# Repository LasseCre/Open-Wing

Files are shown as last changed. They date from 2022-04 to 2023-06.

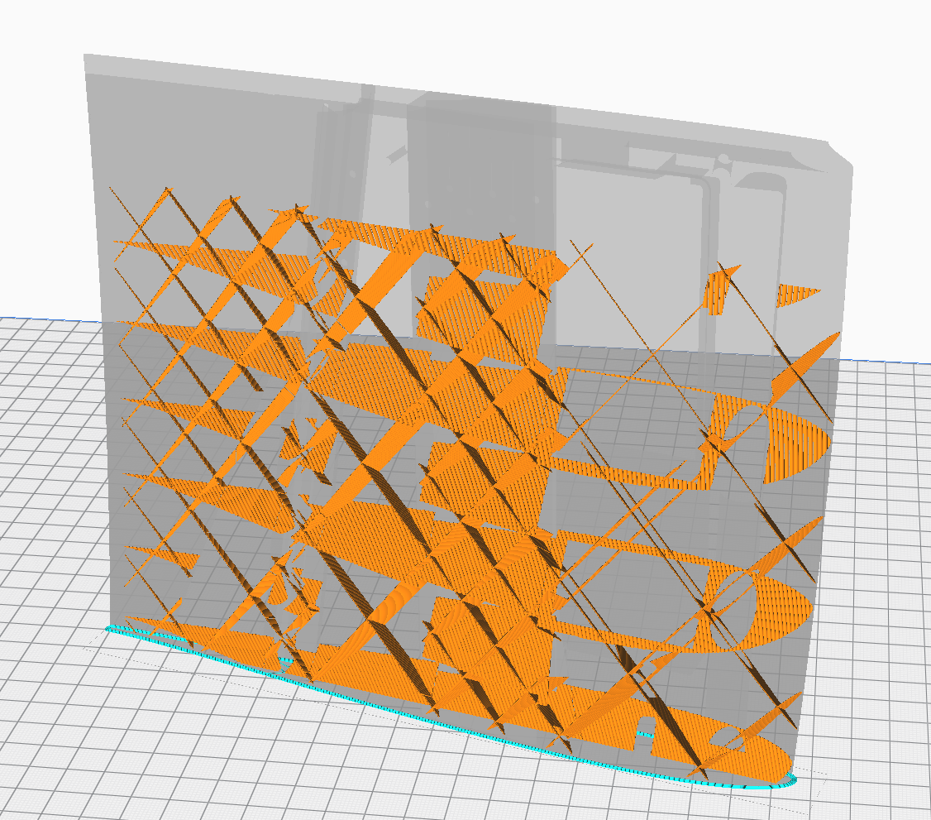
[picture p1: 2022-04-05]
General Data/Images/Cura Screenshot First Mesh Modifier_Infill only.png

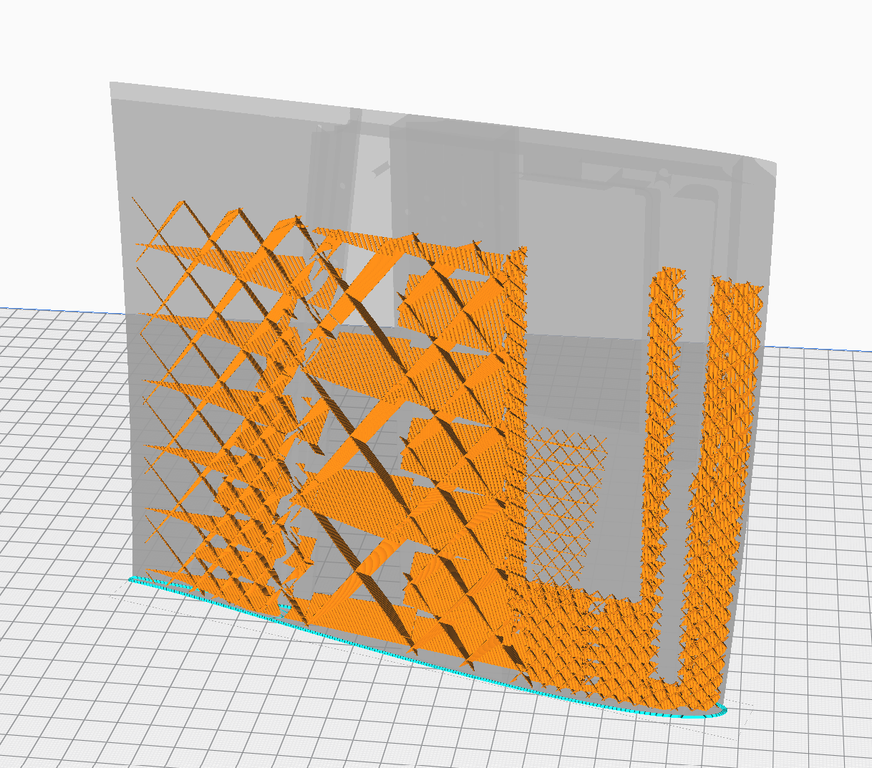
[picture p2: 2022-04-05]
General Data/Images/Cura Screenshot Third Mesh Modifier_Infill only.png

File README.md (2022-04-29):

# Open-Wing
## Documentation for a 3D printable open source rc glider
-----------------------------------------------------------------------------------------------------------
### Related Links:  
Thread in RCN: https://www.rc-network.de/threads/open-wing-ein-2m-allrounder-f%C3%BCr-jede-gelegenheit.11897828/  
Youtube Video: https://www.youtube.com/watch?v=wmPPW6raG3g&ab_channel=LasseC  
Contact me by opening an Issue here, or leave me a message at RC-Network or RC-Groups...  

### Overview
This is (becoming) the complete documentation for a 3d printable flying wing, including all the information that you need to print and build one yourself.
I recommend to read the general [Manual]('0_General%20Data/General%20Manual.md') before you start printing.

Style: Slightly swept plank  
Wingspan: 2000mm  
Weight: 1150 - 1600g (Depending on Configuration)  
Wingloading: 32g/dm^2 - 43g/dm^2  
Material: PLA
Print Time: Approx. 10 Days  
Small transport size (three part wing)  
Quadroflap  
Lots of carbon reinforcement  
Sailplane for now  
(Motor pod might be added later)  

### Structure
There are different versions available which differ in weigth and components, but they all share the same aerodynamic body.  
Therefore the data in the project is structured as follows:  

- **0_General Data** | *Everything that applies to all Versions*
- **V3_Slope** | *Sturdy and a little heavier, perfect for sloping and high speeds - Everything Ready!*
- **V4_Allround** | *The perfect wing to fly all the time, my personal favourite! - Available on demand*
- **V5_Convenience** | *Some measures taken, to make printing and assembly as easy as possible! - In Progress!*  
- **X_Deprecated** | *Old data that is kept only for nostalgic reasons*  

Please note that the Plane was previously called "Oso", which is still apparent in some of the file names  
This is a private project!

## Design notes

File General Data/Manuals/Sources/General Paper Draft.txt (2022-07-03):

OpenWing

Konstruktion und Bau von 3D-gedruckten Nurflügeln am Beispiel eines 2 Meter Seglers

3D-Druck stellt eine neue Fertigungsmethode dar, die in vielen Anwendungsbereichen neue Lösungen verspricht, so auch im Modellbau. Wie bei allen anderen Herstellungsmethoden gibt es jedoch verschiedene Vor- und Nachteile, die bei der Konstruktion möglichst gut ausgespielt, bzw. abgefangen werden sollten. In den letzten vier Jahren habe ich zahlreiche Nurflügelmodelle für die Herstellung mittels 3D-Druck konstruiert, gebaut und getestet, und möchte im folgenden meine Erfahrungen im Bezug auf dieses Herstellungsverfahren schildern. Der Fokus liegt hierbei eher darauf einen möglichen Weg zu zeigen, mit dem alltagstaugliche Modelle entstehen können, als darauf alle möglichen Konstruktionswege und 3D-Druckverfahren abzudecken.
Hierfür möchte ich am Beispiel des OpenWings, einem leicht gepfeiltem 2m Brett, den kompletten Ablauf von Konstruktion bis Erstflug einmal durchgehen. Die aerodynamische Auslegung von Nurflügeln wird nicht mit beschrieben, das vorliegen eines fertigen Entwurfs ist die Ausgangsvoraussetzung für den hier beschriebenen Ablauf.

Hier ein grober Überblick der verwendeten Parameter:
Nurflügelmodelle mit einer Spannweite von 900mm - 2000mm
Gewicht zwischen 250g - 2000g
Vorwiegend Segler (ohne Rumpf)

Fertig vorliegende aerodynamische Auslegung
Konstruktion mittels parametrischem CAD
Klassische Elektronik aus dem Modellbau
Herstellung mittels FDM Drucker
Materialmix aus PLA und CFK verstärkungen

Warum sollte man überhaupt ein Modell 3D-Drucken?
Das Bauen von Flugzeugen mittels 3D-Druck bietet einige Eigenschaften, die in ihrer Kombination interessante Vorteile gegenüber anderen Bauweisen bieten. So können mit 3D-Druck beispielsweise 3D-gekrümmte Oberflächen präziser als beim Positiv- oder Rippenbau hergestellt werden, ohne dabei den Kosten- und Arbeitsaufwand wie beim Bau aus Formen mit sich zu bringen. Außerdem lassen sich im 3D-Druck viele geometrische Features direkt im CAD umsetzen, so dass beim Aufbau wesentliche Arbeitsschritte, wie beispielsweise das Fräsen von Gestängedurchbrüchen, das Einkleben von Servorahmen, oder das Positionieren von Holmgurten, entfallen. Ein weiterer Aspekt ist, dass Dateien einfach ausgetauscht werden können, und somit die Zusammenarbeit and einem Projekt, oder auch das Nachbauen von Flugzeugen, global möglich wird. (Hierbei gibt es allerdings Einschränkungen durch die Verfügbarkeit von Anbauteilen, so sind zum Beispiel zöllische Schraueben oder CFK-Profile in Deutschland nur schwierig zu kriegen)
Andererseits gibt es jedoch auch einige wesentliche Nachteile, wie zum Beispiel die Einschränkungen, die durch die verfügbaren Materialien entstehen. Zumindest im FDM Druck lassen sich nur thermoplastische Kunststoffe (wenn auch teilweise mit kurzfaser Verstärkungen) drucken, bei denen das Verhältnis von Gewicht zu Festigkeit deutlich schlechter ist, als dies zum Beispiel bei CFK oder auch Fichtenholz oder Balsaholz, der Fall ist. Außerdem müssen alle wesentlichen geometrischen Oberflächen bereits im CAD mit konstruiert werden, da spontane Änderungen am fertigen Modell oft nur sehr schwer sauber umzusetzen sind.

Zusammengefasst nochmal die Vor- und Nachteile:
3D-gekrümmte Oberflächen können mit hoher Präzision hergestellt werden
Die Werkzeuge und das Verfahren sind sehr günstig
Es können sehr einfach Einzelstücke gebaut werden
3D-gedruckte Materialien haben ein schlechtes Gewichts / Festigkeitsverhältnis
3D-gedruckte Materialien sind sehr hitzeempfindlich

Um diese Frage zu beantworten, muss man sich die verschiedenen alternativen anschauen, von denen alle ihre Vor- und Nachteile haben, wobei natürlich auch persönliche Parameter, wie das Vorhandensein eines Druckers, oder eben einer Fräse, eine Rolle spielen. Wenn man bei der Arbeit eh eine 5-Achs Fräse stehen hat, die am Wochenende aus riesigen Alu-Reststücken perfekte Formen fräsen kann, und außerdem schon geübt im Umgang mit Faserverbundwerkstoffen ist, so ist 3D-Druck eher uninteressant. Wenn man jedoch eh einen 3D-Drucker hat und verschiedene Auslegungen vergleichend testen möchte, bevor man einen teuren Formensatz fräsen lässt, dann bietet sich 3D-Druck als günstige Testbauweise an. 

Um eine Einschätzung zu ermöglichen, habe ich verschiedene wesentliche Bauweisen in einer Tabelle zusammengefasst und nach mehreren Parametern bewertet. Hierbei wird sowohl die Konstruktion als auch der Bau betrachtet, notwendige Software wird als Werkzeug gewertet.

Parameter:
Einstiegshürden Material: Welche Werkzeuge / Anlagen sind notwendig?
Einstiegshürden Wissen: Wie schwierig ist der Bau, bzw. der Umgang mit den Werkzeugen?
Performance strukturell: Wie gut ist das Verhältnis von Gewicht zu Festigkeit?
Performance aerodynamisch: Mit welcher Genauigkeit lassen sich komplexe Oberflächen umsetzen?
Kosten + Kostenverlauf: Was kostet das erste Modell, was kosten nachfolgende Modelle?
Reproduzierbarkeit: Wie hoch ist der Aufwand für andere das Modell nachzubauen?
Beeinflussung der Umgebung: Braucht es eine Werkstatt, wird mit toxischen Substanzen gearbeitet?
Klassischer Einsatzbereich: Kurze Zusammenfassung des häufigsten Einsatzbereichs

Verfahren:					Rippe + Folie / Beplankung					EPP und co.					Positivbauweise Styro					Negativbauweise

Einstiegshürden Material: Unterschiedlich, Rippen können mit Freeware Tools gezeichnet und	Geringste Materialvoraussetzungen, fertig geschnittene	Hier ist der Aufwand für die Kerne ähnlich wie	Hohe Einstiegshürden, da allein das Material für				  von Hand geschliffen werden, dann sind jedoch nur einfache		Kerne können nach Maß online bestellt werden.		bei der Bauweise EPP und Co. Allerdings kommt	die Formen mehr kostet als so manches Modell.
			  Geometrieen mit beschränkter Genauigkeit möglich. Alternativ		Auch wenn man selber schneiden will, braucht man	dazu noch die Beschichtung mit einem 		Außerdem braucht man die Möglichkeit ein Urmodell
			  kann auch im CAD konstruiert und anschließend gelasert / gefräst	lediglich Schneidschablonen, einen Hiezdraht und	Faserverbundwerkstoff und / oder Holz, was	oder die Formen selber fräsen zu lassen, hinzu kommt
			  werden, dann braucht es mindestens eine Fräse / Laser, dafür		etwas Übung.						den Einsatz einer (einfachen) Presse oder eines	die manuelle Nachbearbeitung und das meistens eher
			  wird die Vervielfältigung einfacher. Außerdem benötigt man									Vakuumsystems voraussetzt.			teure Material für den Flieger selber.
			  neben "normalem" Werkzeug noch ein Folienbügeleisen.

Einstiegshürden Wissen:	  Gering, für einfache Geometrien ist kaum Vorwissen
			  erforderlich.

Performance strukturell:

Performance aerodynamisch:

Kosten + Kostenverlauf:

Reproduzierbarkeit:

Beeinflussung der Umgebung:

Klassischer Einsatzbereich:

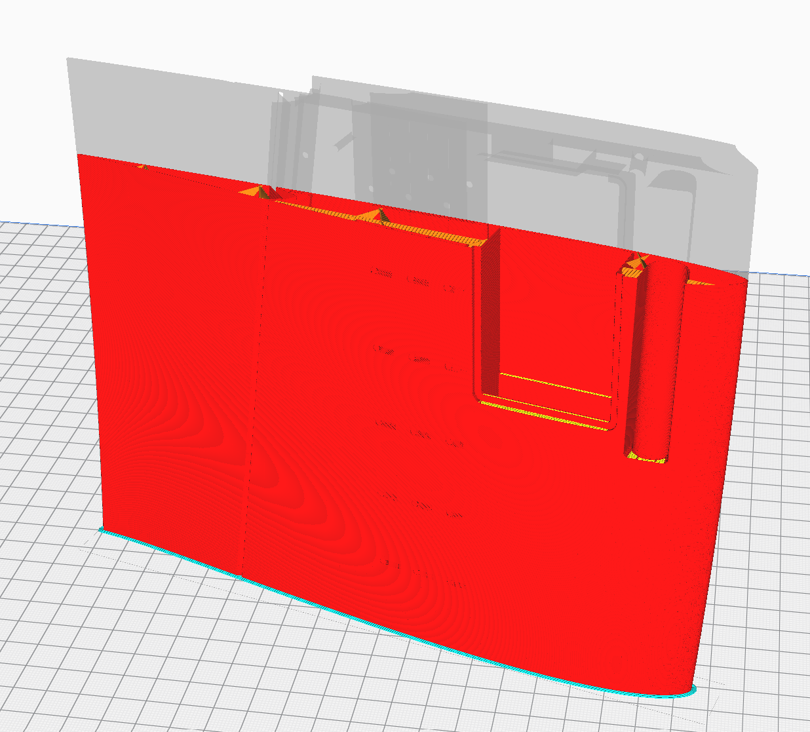
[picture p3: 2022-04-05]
General Data/Images/Cura Screenshot No Mesh Modifier.png

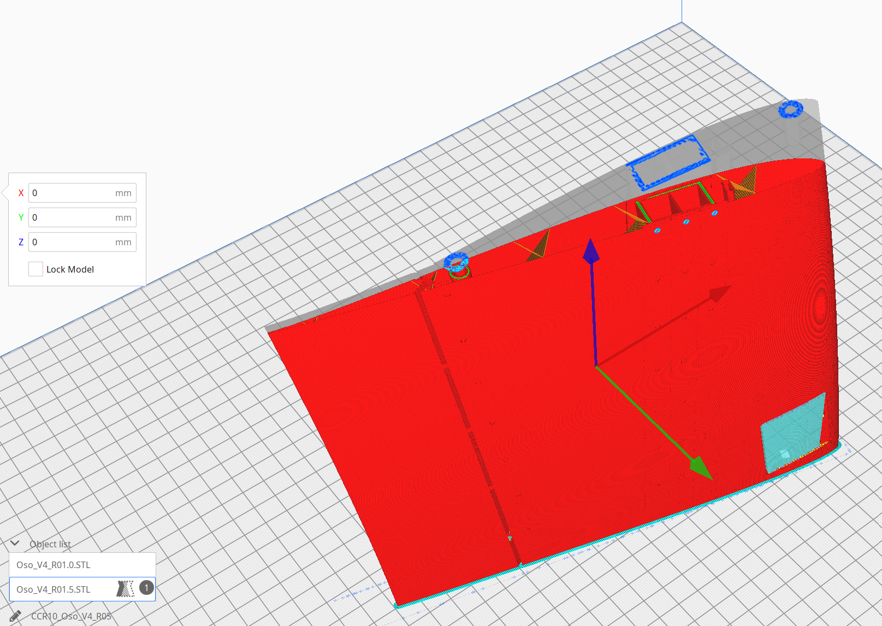
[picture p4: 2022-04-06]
General Data/Images/Two volumes Placement2.png

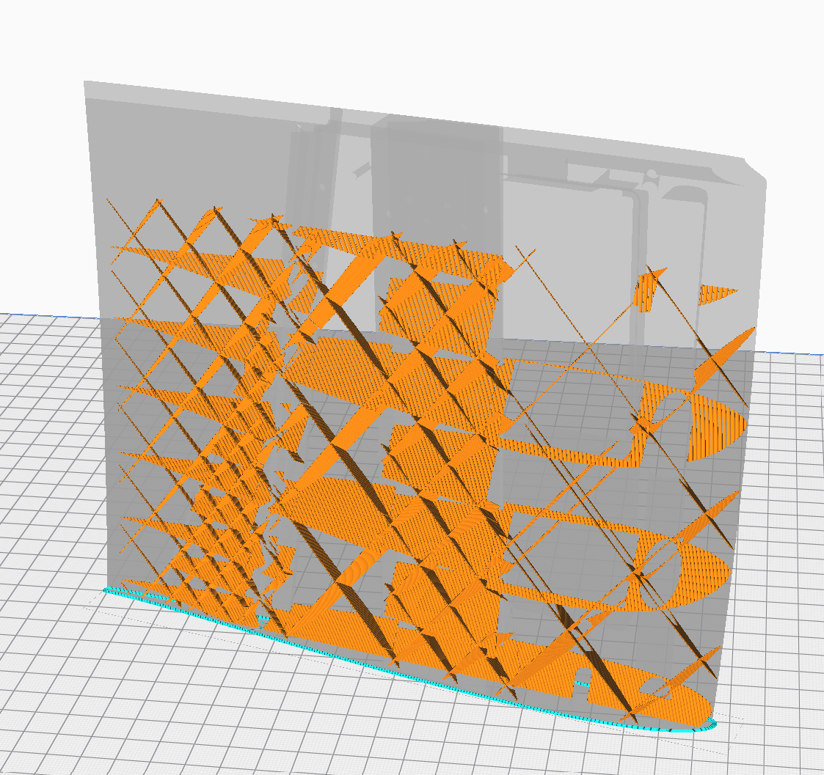
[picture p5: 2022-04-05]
General Data/Images/Cura Screenshot Second Mesh Modifier_Infill only.png

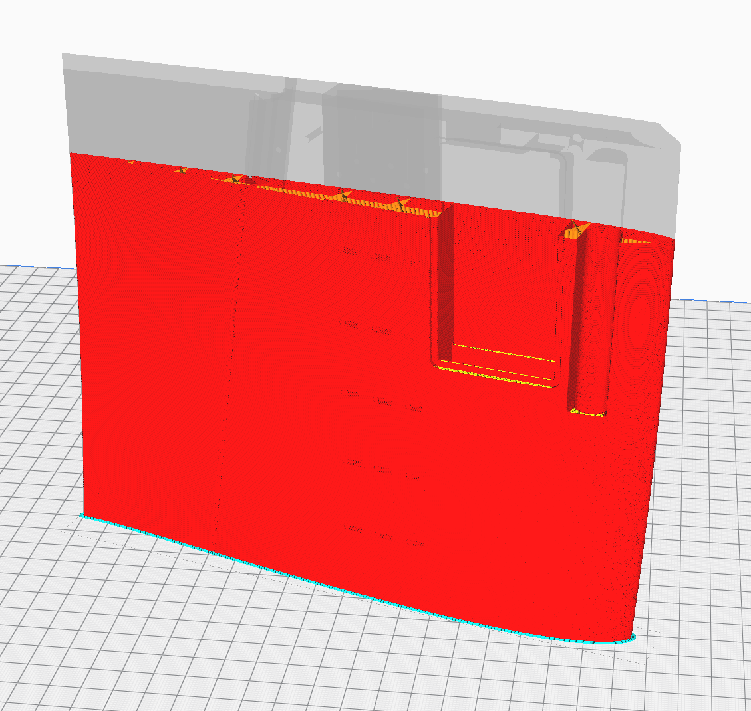
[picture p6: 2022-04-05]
General Data/Images/Cura Screenshot Second Mesh Modifier.png

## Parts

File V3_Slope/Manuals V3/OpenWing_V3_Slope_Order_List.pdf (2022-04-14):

# OpenWing_V3_Slope

### Oder List (EU)

Main spars

Wing joiners

Fuselage and stabilizer

Glue

For hinges

10 Pcs 0.5x10x1000mm rectangular carbon strip

2 Pcs 0.5x3x1000mm rectangular carbon strip

1 Pcs 0.6x5x1000mm rectangular carbon strip

10x10x1000mm rectangular carbon tube

4x100mm carbon tube

10/8x500mm pullwinded carbon tube

3x250mm carbon tube

20g thick CA glue | https://shop1.r-g.de/art/150120 Art.-Nr.: 1501202
2 Pcs 20g thin CA glue | https://shop1.r-g.de/art/150100 Art.-Nr.: 1501002

10 Pcs 1.2mm needles for application

1-3 Pcs syringe

Tape

Silikon (Bindulin Dichtfix) https://shop1.r-g.de/art/330155 Art.-Nr.: 3301552

https://shop1.r-g.de/art/330154
Art.-Nr.: 3301543

https://www.amazon.de/tesa-Malerband-einfache-Malerarbeiten-30mm/dp/B000VD8ZBW/ref=sr_1_5

https://www.amazon.de/Bindulin-Dichtfix-Fl%C3%BCssig-Gummi-Farbe-Com24/dp/B07DMQJTQP/ref=sr_1_16

8x250mm carbon tube

https://shop1.r-g.de/art/720003 Art.-Nr.: 7210005-100

https://shop1.r-g.de/art/720003 Art.-Nr.: 7203005-100

https://shop1.r-g.de/art/720003 Art.-Nr.: 7205006-100

https://shop1.r-g.de/art/750302 Art.-Nr.: 7510091

https://shop1.r-g.de/art/604070
Art.-Nr.: 64040030-100

https://www.carbonscout-shop.de/CFK-Carbon-Rohr-10x8x1000mm-Pullwinding.html

https://shop1.r-g.de/art/604070 Art.-Nr.: 64030020-100

https://shop1.r-g.de/art/604070 Art.-Nr.: 64080060-050

1/2

# OpenWing_V3_Slope

### Oder List (EU)

2/2

Electronics

Servo connections

Ballast Material

Option:
4 Pcs KST X10-mini

Option:
4 Pcs Kingmax 0612W 10mm HV-Servo

Option:
4 X-612 Servo

Y cable for batteries

2 Pcs battery for 2S2P

4 Pcs Cables for Servos

4 Pushrod M2

4 Pcs „Alu Gabelkopf M2“

2-3 Pcs 10x100mm K10 tungsten steel https://www.f3x.de/kst-x10-mini-v8-10mm-digitaleshv-servo-bis-75-ncm

https://www.mg-modellbau.de/Servos/Kingmax/Servo-Kingmax-10mm-HV-Servo-54-85kgcm-50-84V-Digital-Uni-Stecker.html
https://www.f3x.de/x-612-10mm-hv-servo-bis-85-ncm-coreless-digital

https://www.conrad.de/de/p/modelcraft-parallel-kabel-1x-bec-buchse-2x-bec-stecker-10-00-cm-0-25-mm-208423.html

https://www.conrad.de/de/p/reely-modellbau-akkupack-lipo-7-4-v-600-mah-zellen-zahl-2-15-c-softcasebec-buchse-1614803.html

https://www.amazon.de/YIXISI-Verl%C3%A4ngerungskabel-Stecker-Fernbedienung-Flugzeug/dp/B08JVBYS8L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

https://www.f3x.de/alu-gabelkopf-23mm-gewindem2

https://www.ebay.de/itm/402851236392https://www.f3x.de/stahl-schubstange-1,7-mm-x-200-mm-mit-teilgewinde-m2

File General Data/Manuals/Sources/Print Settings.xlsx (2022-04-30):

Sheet: Printsettings_General
Layer Height | 0.16
Line Width | 0.38
Wall line count | 1
Top Layers | 2
Bottom Layers | 2
Outer before inner walls | X
Compensate wall overlaps | X
Compensate inner wall overlaps | X
Compensate outer wall overlaps | X
Fill gaps between walls | Nowhere
Infill before walls | OFF!
Infill overlap percentage | -35%
Z-Hop when retracted | X
Z-Hop height | 0.4
Support | X
Build plate adhesion | Brim
Brim line count | 4

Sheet: Printsettings_V3_Slope
Part | Main | Modifier | Width | Wall count | Infill | Top | Bottom | Weight (L+R)
R05.0 | X |  | 0.38mm | 1 | 3.50% | 2 | 2 | 37g
R05.1 |  | X |  |  | 7%
R05.2 |  | X |  | 1 | 14%
R04.0 | X |  | 0.38mm | 1 | 3.50% | 2 | 2 | 80g
R04.1 |  | X |  |  | 7%
R04.2 |  | X |  |  | 14%
R04.3 |  | X |  | 1 | 14%
R03.0 | X |  | 0.38mm | 1 | 3.50% | 2 | 2 | 141g
R03.1 |  | X |  |  | 7%
R03.2 |  | X |  |  | 14%
R03.3 |  | X |  | 1 | 14%
R03.4 |  | X |  | 2 | 28% | 2 | 2
R03.Block |  | Support Blocker
R02.0 | X |  | 0.38mm | 1 | 3.50% |  |  | 170g
R02.1 |  | X |  |  | 7% | 1
R02.2 |  | X |  |  | 14%
R02.3 |  | X |  | 2 | 14% | 2
R02.4 |  | X |  | 100
R01.0 | X |  | 0.38mm | 1 | 3.50% |  |  | 207g
R01.1 |  | X |  |  | 7% | 1
R01.2 |  | X |  |  | 14%
R01.3 |  | X |  | 3 | 28% | 5 | 5
R01.4 |  | X |  | 100
R01.Block |  | Support Blocker
R00.0 | X |  | 0.38mm | 1 | 3.50% |  |  | 245g
R00.1 |  | X |  |  | 7% | 1
R00.2 |  | X |  |  | 14%
R00.3 |  | X |  | 3 | 28% | 5 | 5
R00.4 |  | X |  | 100
SLW00.0 | X |  | 0.38mm | 1 | 3%
SLW00.1 |  | X |  |  | 6%
SLW01.0 | X |  | 0.38mm | 1 | 3%
SLW01.1 |  | X |  |  | 6%
Covers | X |  | 0.4mm | 1 | 10% | 4 | 2
Servo Horns | X |  | 0.4mm | 50
Helling | X |  | 0.4mm | 2 | 10% | 4 | 4

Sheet: Printsettings_V5_Community
Part | Main | Modifier | Width | Wall count | Infill | Top | Bottom | Weight (L+R)
R05.0 | X |  | 0.38mm | 1 | 3.00% | 2 | 2 | 34g
R05.1 |  | X |  |  | 6%
R05.2 |  | X |  |  | 12%
R04.0 | X |  | 0.38mm | 1 | 3.00% | 2 | 2 | 75g
R04.1 |  | X |  |  | 6%
R04.2 |  | X |  |  | 12%
R04.3 |  | X |  |  | 12%
R03.0 | X |  | 0.38mm | 1 | 3.00% | 2 | 2 | 139g
R03.1 |  | X |  |  | 6%
R03.2 |  | X |  |  | 12%
R03.3 |  | X |  | 2 | 24% | 2 | 2
R03.Block |  | Support Blocker
R02.0 | X |  | 0.38mm | 1 | 3.00% |  |  | 164g
R02.1 |  | X |  |  | 6% | 1
R02.2 |  | X |  |  | 12%
R02.3 |  | X |  | 2 | 12% | 2 | 2
R02.4 |  | X |  | 3 | 36% | 2 | 2
R01.0 | X |  | 0.38mm | 1 | 3.00% |  |  | 191g
R01.1 |  | X |  |  | 6% | 1
R01.2 |  | X |  |  | 12%
R01.3 |  | X |  | 2 | 24% | 2 | 2
R01.4 |  | X |  | 3 | 36% | 2 | 2
R01.Block |  | Support Blocker
R00.0 | X |  | 0.38mm | 1 | 3.00% |  |  | 203g
R00.1 |  | X |  |  | 6% | 1
R00.2 |  | X |  |  | 12%
R00.3 |  | X |  | 2 | 24% | 2 | 2
R00.4 |  | X |  | 100
SLW00.0 | X |  | 0.35mm | 1 | 3% |  |  | Complete 24g
SLW00.1 |  | X |  |  | 6%
SLW01.0 | X |  | 0.35mm | 1 | 3%
SLW01.1 |  | X |  |  | 6%
Covers | X |  | 0.38mm | 1 | 20% | 2 | 2 | 20g
Servo Horns | X |  | 0.38mm | 50
Helling | X |  | 0.4mm | 2 | 10% | 4 | 4

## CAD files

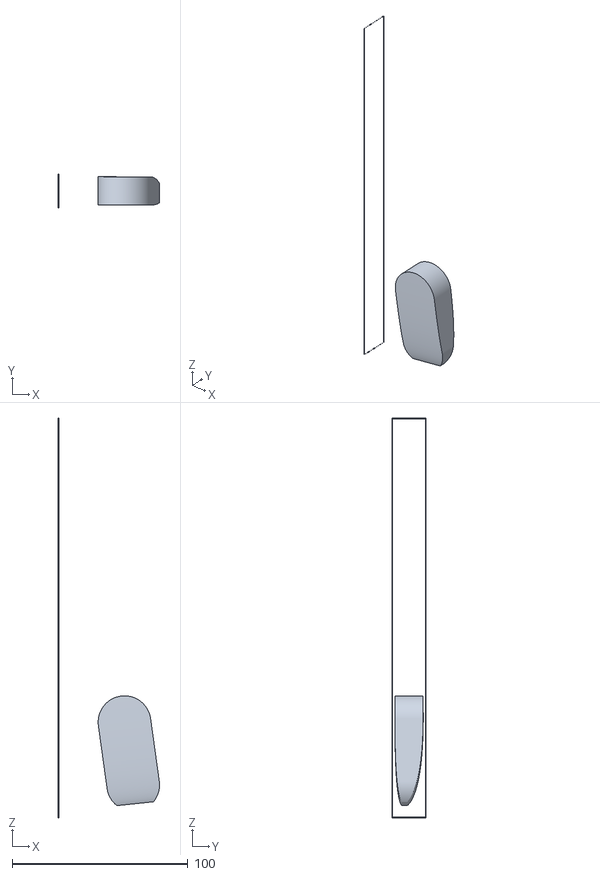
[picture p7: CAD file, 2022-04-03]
CAD/Export/V1/Oso_R01/Oso_R01.6.STL
57.5 x 19.0 x 227.0

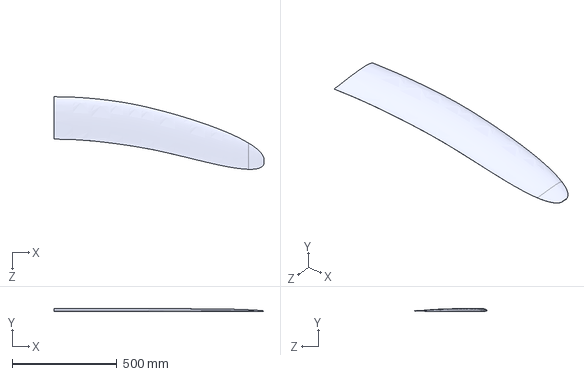
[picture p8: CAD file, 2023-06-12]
General Data/3D/OpenWing_Clean Volume.STEP
1000.0 x 16.4 x 346.0 mm

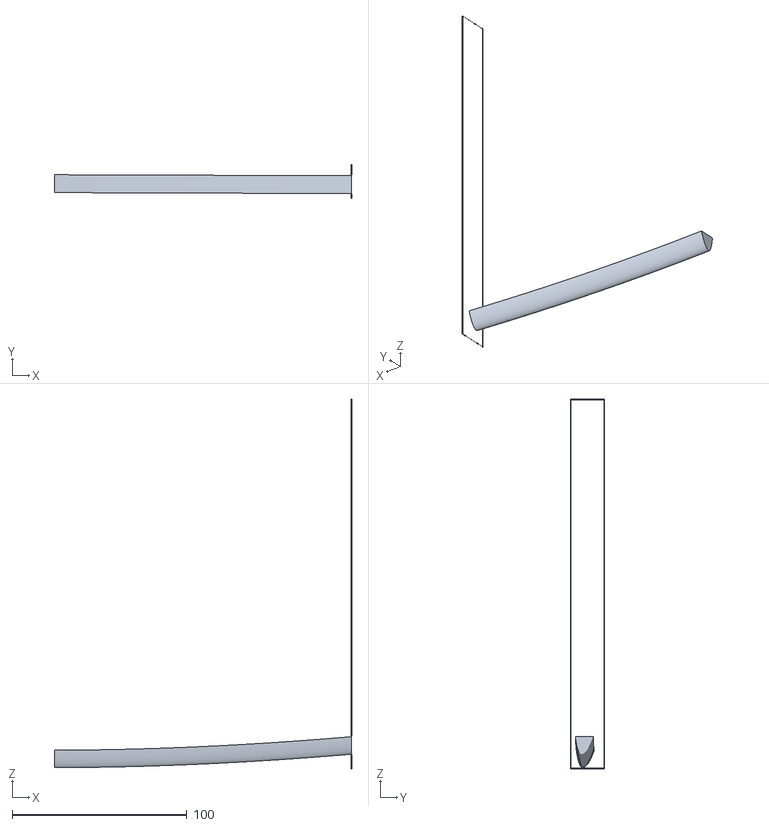
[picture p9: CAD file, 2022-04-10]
V3_Slope/3D/STL/OpenWing_V3_Slope_R00/OpenWing_V3_Slope_R00.4.STL
170.0 x 19.0 x 211.0

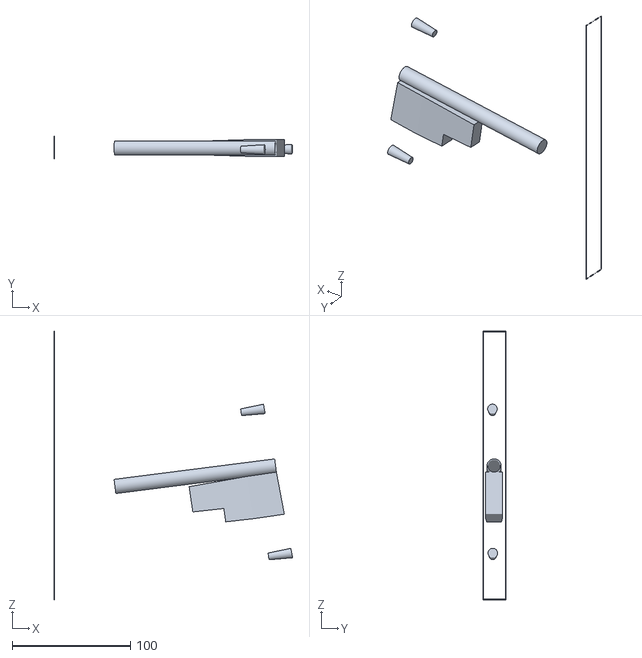
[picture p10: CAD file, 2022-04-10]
V3_Slope/3D/STL/OpenWing_V3_Slope_R01/OpenWing_V3_Slope_R01.4.STL
201.9 x 19.0 x 227.0

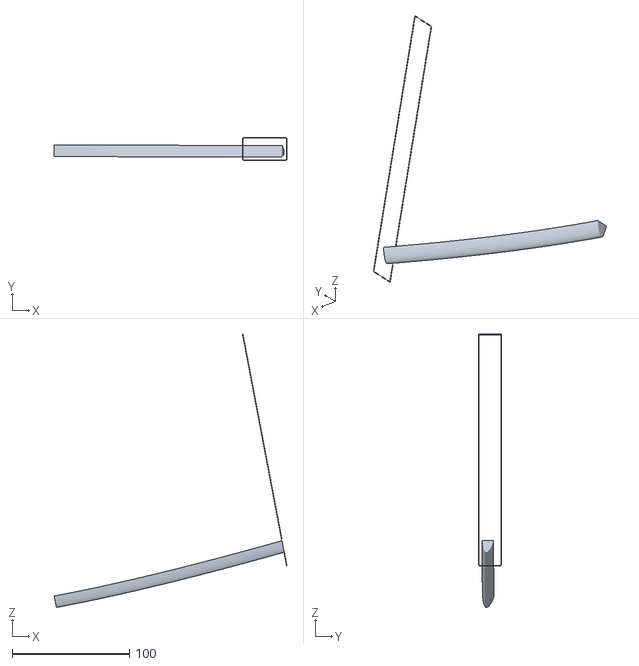
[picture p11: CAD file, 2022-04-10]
V3_Slope/3D/STL/OpenWing_V3_Slope_R02/OpenWing_V3_Slope_R02.3.STL
198.7 x 19.0 x 233.1

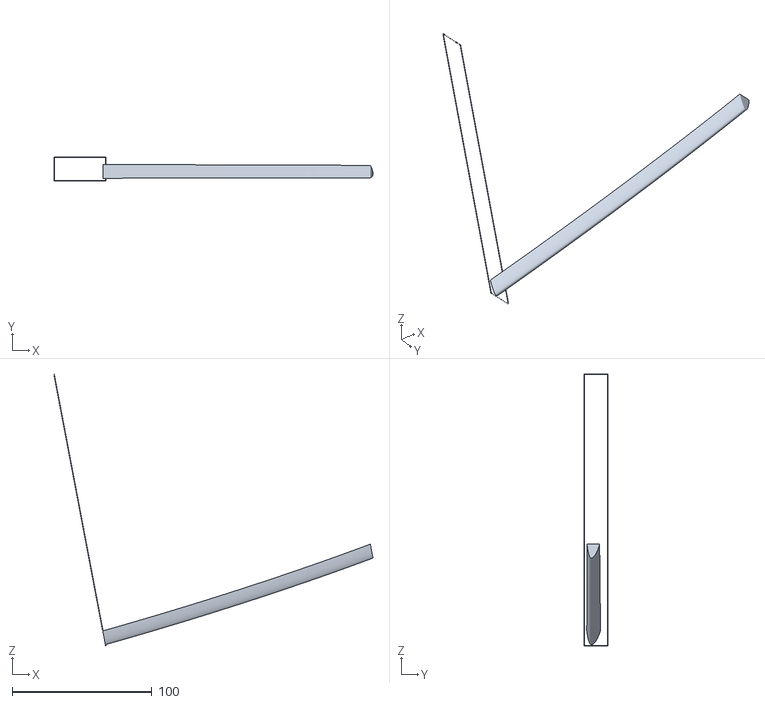
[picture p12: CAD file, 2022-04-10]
V3_Slope/3D/STL/OpenWing_V3_Slope_R03/OpenWing_V3_Slope_R03.3.STL
228.6 x 17.0 x 194.6

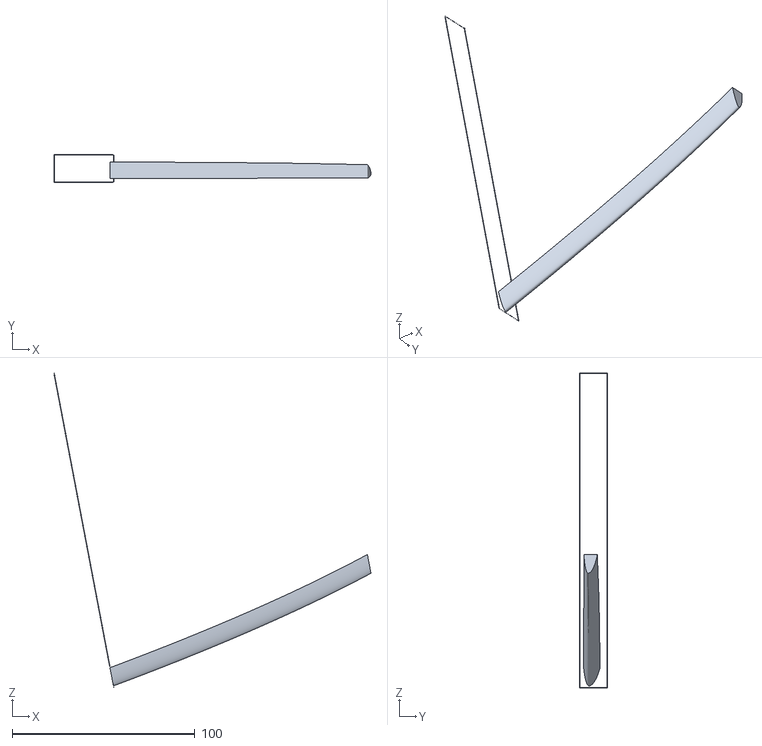
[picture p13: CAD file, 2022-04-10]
V3_Slope/3D/STL/OpenWing_V3_Slope_R04/OpenWing_V3_Slope_R04.3.STL
173.5 x 15.0 x 172.0

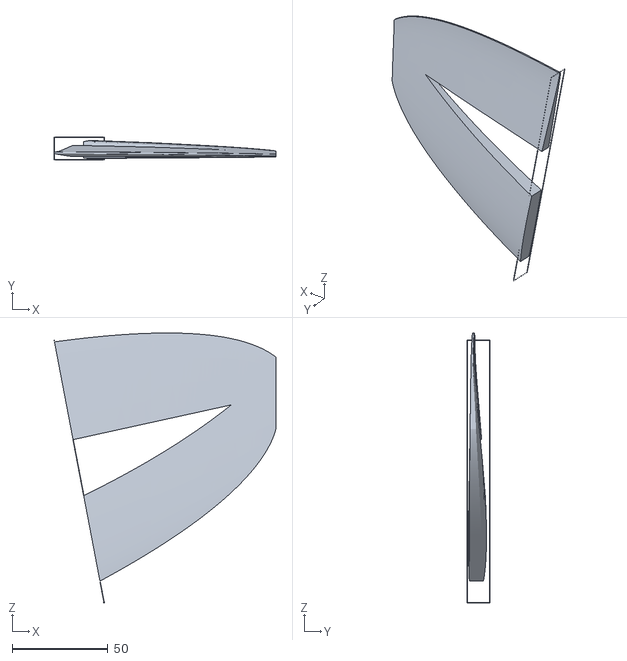
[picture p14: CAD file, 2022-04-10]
V3_Slope/3D/STL/OpenWing_V3_Slope_R05/OpenWing_V3_Slope_R05.1.STL
116.0 x 12.0 x 141.2

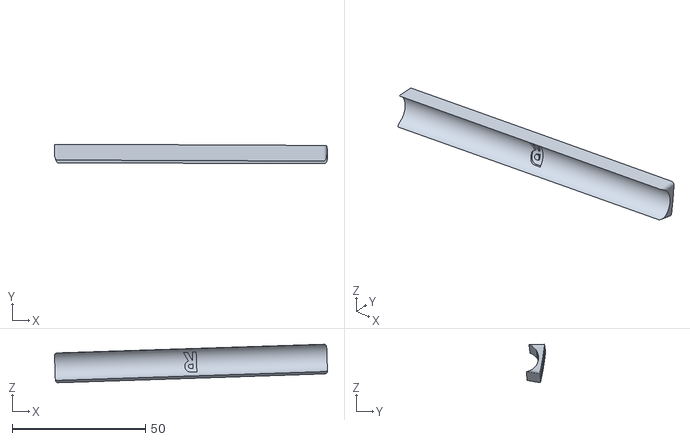
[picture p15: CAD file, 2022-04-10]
V3_Slope/3D/STL/OpenWIng_V3_SLope_SmallParts/OpenWing_V3_Slope_BallastCover.STL
102.4 x 7.13 x 14.5

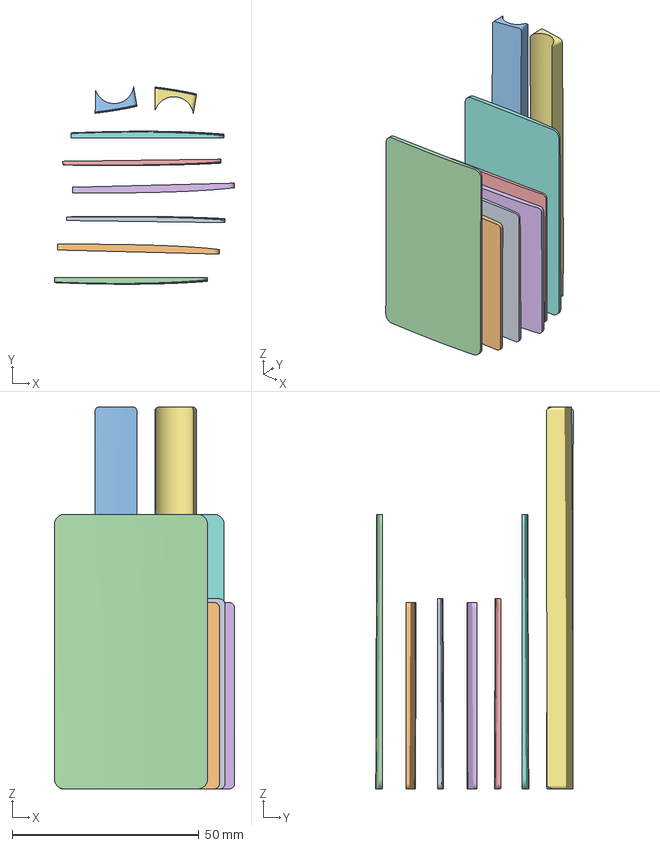
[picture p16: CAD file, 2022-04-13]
V3_Slope/Print/OpenWing_V3_Slope_CuraFiles/OpenWing_V3_Slope_Covers.3mf
48.2 x 52.9 x 102.2 mm
OpenWing_V3_Slope_ServoCover1.STL
OpenWing_V3_Slope_ServoCover0.STL
OpenWing_V3_Slope_BallastCover.STL
OpenWing_V3_Slope_ComponentCover.STL
OpenWing_V3_Slope_ServoCover1.STL(1)
OpenWing_V3_Slope_ServoCover0.STL(1)
OpenWing_V3_Slope_BallastCover.STL(1)
OpenWing_V3_Slope_ComponentCover.STL(1)

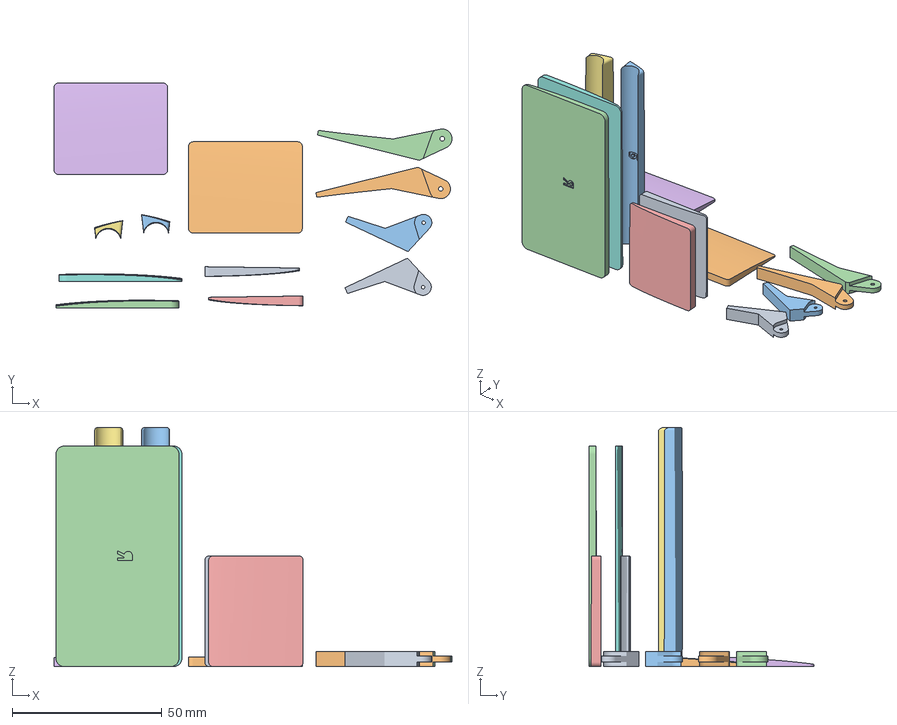
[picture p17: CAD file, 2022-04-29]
V4_Allround/V4.0_Allround/Print/Cura Files/OpenWing_V4_Small Parts.3mf
132.7 x 75.0 x 79.7 mm
Servodeckel_R1.STL
Servodeckel_R2.STL
Ballastdeckel_R.STL
Komponentendeckel_R.STL
Servodeckel_R1.STL(1)
Servodeckel_R2.STL(1)
Ballastdeckel_R.STL(1)
Komponentendeckel_R.STL(1)
Ruderhorn Aussen.STL
Ruderhorn Innen.STL
Ruderhorn Aussen.STL(1)
Ruderhorn Innen.STL(1)

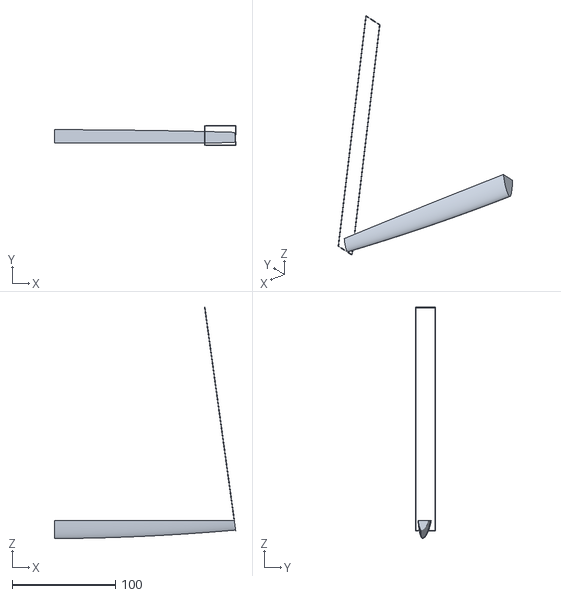
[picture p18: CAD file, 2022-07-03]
V4_Allround/V4.1_Allround_Light/3D/STLs/R00/OpenWing_V4.1_R00.4.STL
175.7 x 19.0 x 223.6

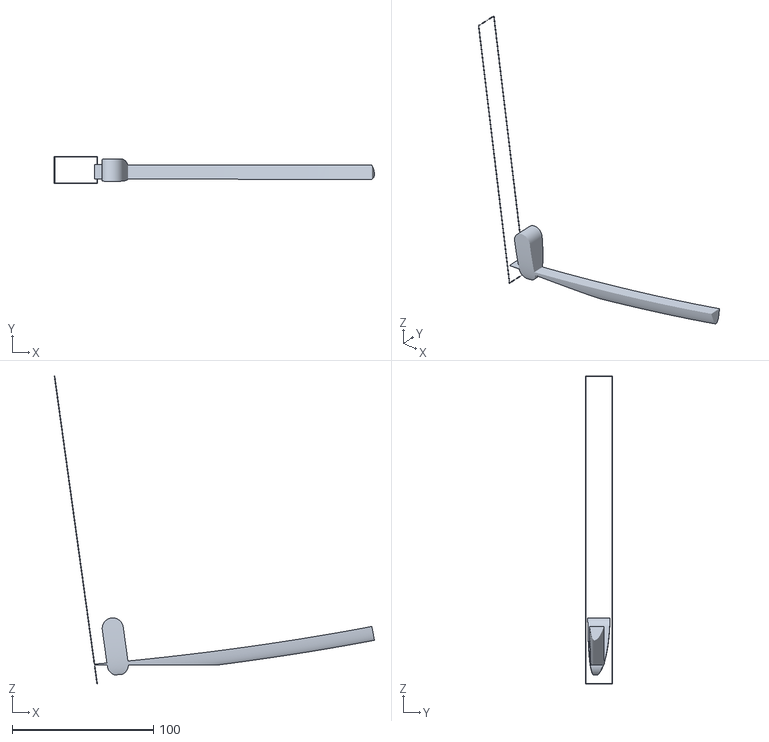
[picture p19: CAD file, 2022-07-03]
V4_Allround/V4.1_Allround_Light/3D/STLs/R01/OpenWing_V4.1_R01.3.STL
226.9 x 19.0 x 218.0

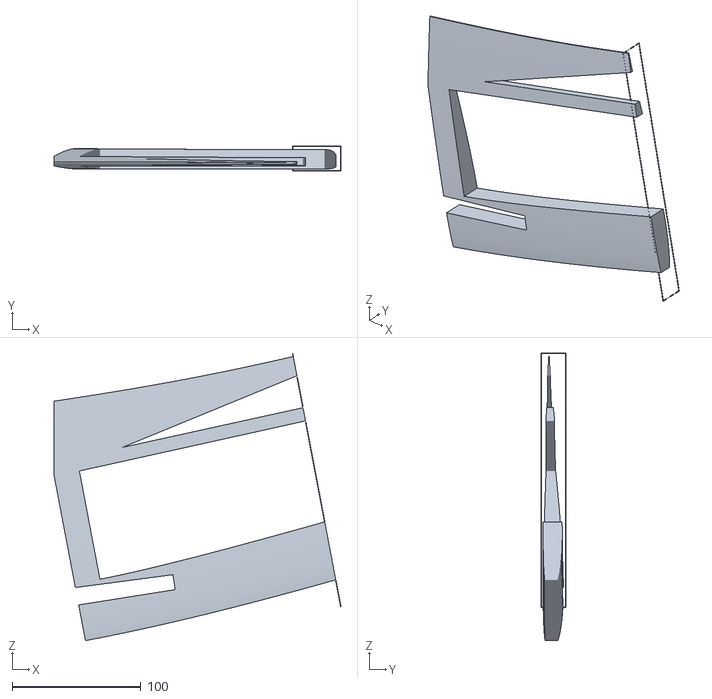
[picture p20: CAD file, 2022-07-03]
V4_Allround/V4.1_Allround_Light/3D/STLs/R02/OpenWing_V4.1_R02.1.STL
223.1 x 19.0 x 223.3

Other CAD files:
V4_Allround/V4.1_Allround_Light/3D/STLs/R03/OpenWing_V4.1_R03.2.STL
V4_Allround/V4.1_Allround_Light/3D/STLs/R04/OpenWing_V4.1_R04.2.STL
V4_Allround/V4.1_Allround_Light/3D/STLs/R05/OpenWing_V4.1_R05.2.STL
V4_Allround/V4.2_Allround_Superlight/3D/STLs/Helling 3°/OpenWing_V4.2_Allround_Helling3°_R00.STL
CAD/Export/V1/Oso_R01/Oso_R01.5.STL
V3_Slope/3D/STL/OpenWIng_V3_SLope_SmallParts/OpenWing_V3_Slope_ComponentCover.STL
V3_Slope/3D/STL/OpenWIng_V3_SLope_SmallParts/OpenWing_V3_Slope_ControlHorn0.STL
V3_Slope/3D/STL/OpenWIng_V3_SLope_SmallParts/OpenWing_V3_Slope_ControlHorn1.STL
V3_Slope/3D/STL/OpenWIng_V3_SLope_SmallParts/OpenWing_V3_Slope_ServoCover0.STL
V3_Slope/3D/STL/OpenWIng_V3_SLope_SmallParts/OpenWing_V3_Slope_ServoCover1.STL
V3_Slope/3D/STL/OpenWing_V3_Slope_R00/OpenWing_V3_Slope_R00.1.STL
V3_Slope/3D/STL/OpenWing_V3_Slope_R00/OpenWing_V3_Slope_R00.2.STL
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

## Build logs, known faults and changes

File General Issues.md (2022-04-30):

**The things that get done soon:**  
- Fix the bug in V3 Cura files  
- Writing a general manual for slicing with pictures  
- Write the first build manual with pictures (Video maybe?)  
- Start working on the Documentation for V4  
- Start working on V6_Ultralight  

Changes 30.04.2022:  
- Export the STLs for V5  
- Slice V5  
- Document the Print settings for V5  

**Useful Ideas to implement:**  
How to print the cutouts for the servos without suppert...?

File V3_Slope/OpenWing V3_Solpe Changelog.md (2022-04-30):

# OpenWing_V3_Slope

## Changelog:  

30.04.22 V3_Slope  
3mf files and GCodes have been fixed for R00 (R+L) and R01 (R+L)  

Known Issues:  
Update on mistakes in Printfiles: STRG+Z does not work as expected in Cura, 3mf Files and GCodes are broken.  
~~Mistake in printing oder in cura file "CCR10_OpenWing_V3_Slope_InnerWing.3mf", maybe also in depending G-Code Files - Check and Correct!~~  
~~(Panel R01.0, Right side...)~~  

14.04.2022 V3_SLope  
Added Naming on Helling Parts  
Exported Helling Parts
Added Cura Files of all parts  
Added G-Codes of all parts  
Uploaded new Order List with ballast Material  
~~NOT YET TESTED!~~
Test in Progress  

Known Issues:  
~~Ballast Material missing in Order List~~    
~~Helling Parts should have names on them!~~    
~~Cura files / slicing needs to be done~~    
~~Gcodes need to be exported~~  

10.04.2022 V3_Slope  
Changed V3.1 and V3 to V3_Slope   
Changed fuselage diameter from 9.5mm for BRUXX Arrowshaft back to 10.5mm for proper tube  
Added internal tubes for ballast in CG  
Added internal antenna tubes  
Marked covers for identification  
Added Option for fixation on helling parts  

Known Issues:  
~~Missing internal tubes for receiver antenna~~  
~~Missing opportunity for internal ballast in CG~~  

09.04.2022 V3.1  
Height for spar cutouts changed from 0.8mm to 0.7mm  
Width for spar cutouts changed to 10.4mm  
Battery compartment height changed from 11mm to 11.5mm  
Changed CG Holes from 109mm to 109.5mm D1,5mm  
~~Changed fuselage diameter from 10.5mm to 9.5mm for BRUXX Arrowshaft~~   
Changed Servo Cutout for X-612 in width (+0.25mm)  
Widened the hole for the 3mm CF tube in the vertical stabilizer from 3.2mm to 3.25mm  
Cutout for servo wire in R01 was made slightly shallower to make support removal easier  
Glue holes over helling parts removed  
Reduced gluehole size from 2mm to 1mm

~~"Vliesscharniere":~~  
~~Pushed rear spars 10mm forward to make space for them~~  
~~Added the cutouts~~  
~~Increased hinge gaps from 0.4 to 0.8mm~~  

Known Issues:  
~~Cutout for Spars could be a bit smaller~~   
~~Cutout for Servos could be a bit bigger~~  
~~10mm Pullwinded Tube does not have 8mm inner diameter and is hard to get, change to arrow shaft!~~  
~~Glue holes over helling parts~~  
~~Support in R01 is difficult to remove~~  
~~Double launch hole not needed -> Screw fuse solution~~  
~~3mm Hole in VS is to small~~  
~~COG is at 110, not at 113!~~  
~~Glue Holes could be smaller~~  
 
~~Covers are too similar  -> Fix when new Servos are in~~  
VS is too heavy -> Fixing when slicing  

~~Helling could be better -> Self securing~~  

V4:  
Channels for Servo wires dont match between R00 und R01  
Glue Holes could be smaller  
Change CG-Holes to 109.5mm

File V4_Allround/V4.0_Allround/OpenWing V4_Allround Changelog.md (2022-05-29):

# OpenWing_V3_Slope

## Changelog:  

Known Issues:  
Could profit from adding carbon in the flaps and elevons  
Little more space between the inner Flaps and the Carbon Tube  
Maybe add joiner for the rear Carbon strips in the middle  
See if the Servo support can be reduced / removed

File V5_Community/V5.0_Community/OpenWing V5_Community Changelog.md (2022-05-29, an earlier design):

# OpenWing_V5_Community

## Changelog:  

Known Issues:  
Add a feature to hold "Ballastcover" in place, even when no Ballast is used!
Move the wall above the Servo to keep the "Anlenkungsdraht" secured better!

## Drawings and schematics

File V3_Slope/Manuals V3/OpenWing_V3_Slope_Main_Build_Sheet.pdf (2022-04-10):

# OpenWing_V3_Slope

# Wingspan:

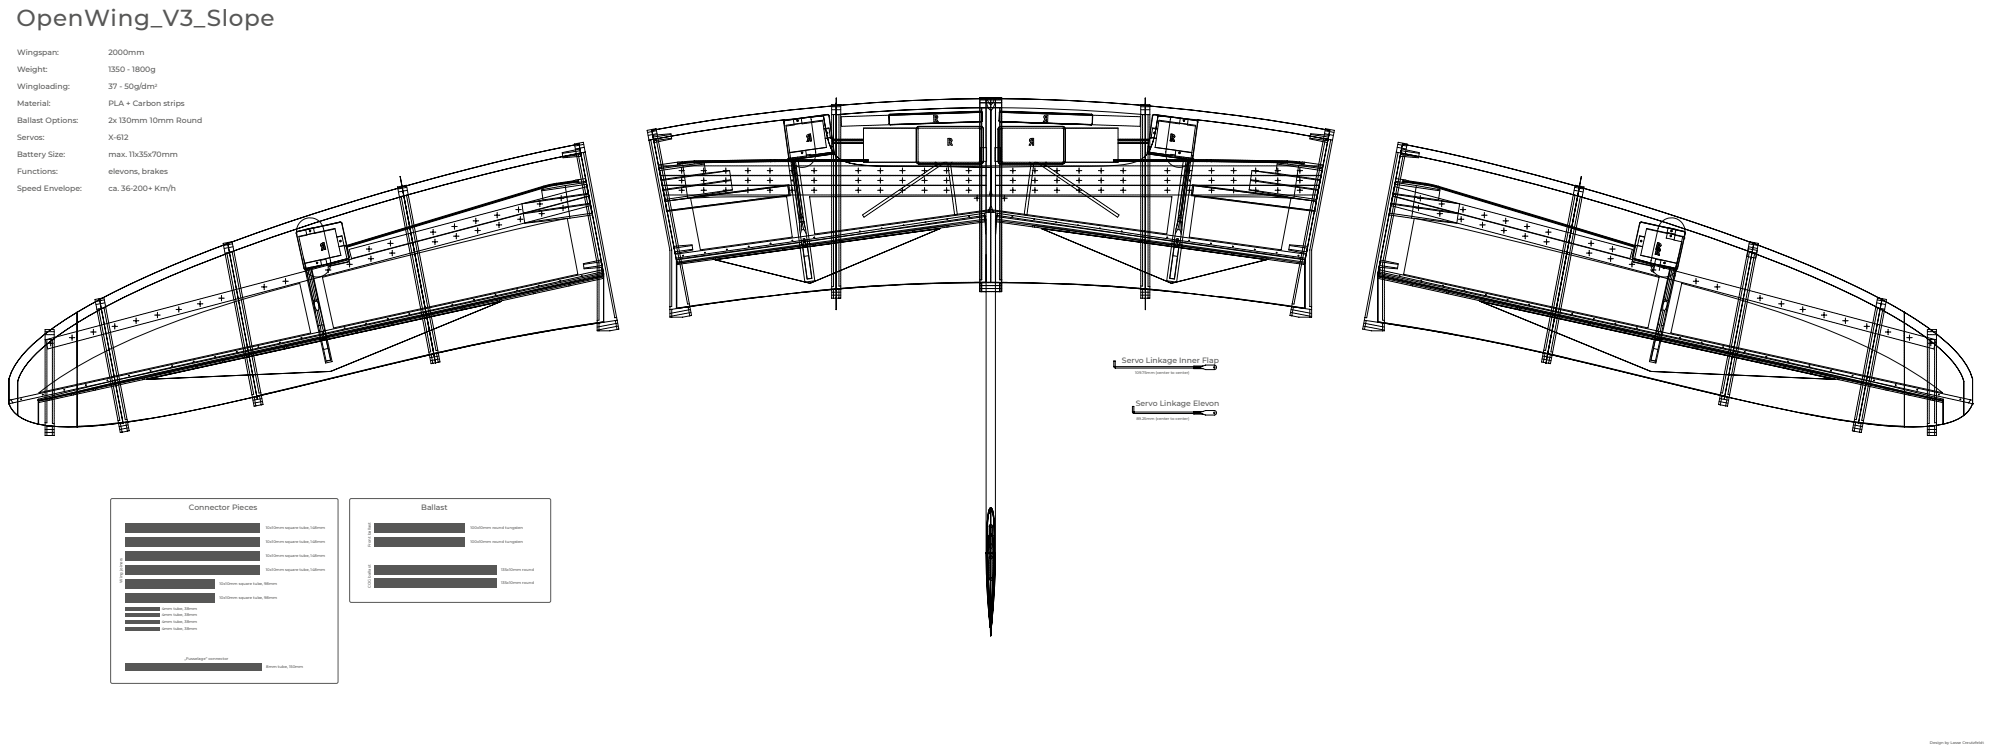
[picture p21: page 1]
Weight:; Wingloading:; Material:; Ballast Options:; Servos:; Battery Size:; Functions:; Speed Envelope:; 37 - 50g/dm²; PLA + Carbon strips; 2x 130mm 10mm Round; max. 11x35x70mm; elevons, brakes; Ballast; 100x10mm round tungsten; 135x10mm round; Connector Pieces; 10x10mm square tube, 148mm; 10x10mm square tube, 98mm; Wing joiners; 4mm tube, 38mm 4mm tube, 38mm 4mm tube, 38mm 4mm tube, 38mm; 8mm tube, 150mm; „Fusselage“ connector

Servo Linkage Inner Flap

109.75mm (center to center)

Servo Linkage Elevon

89.25mm (center to center)

Front ballast COG ballast

Design by Lasse Creutzfeldt

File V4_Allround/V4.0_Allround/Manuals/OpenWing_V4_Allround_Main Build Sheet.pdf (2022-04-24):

# OpenWing_V4_Allround

# Wingspan:

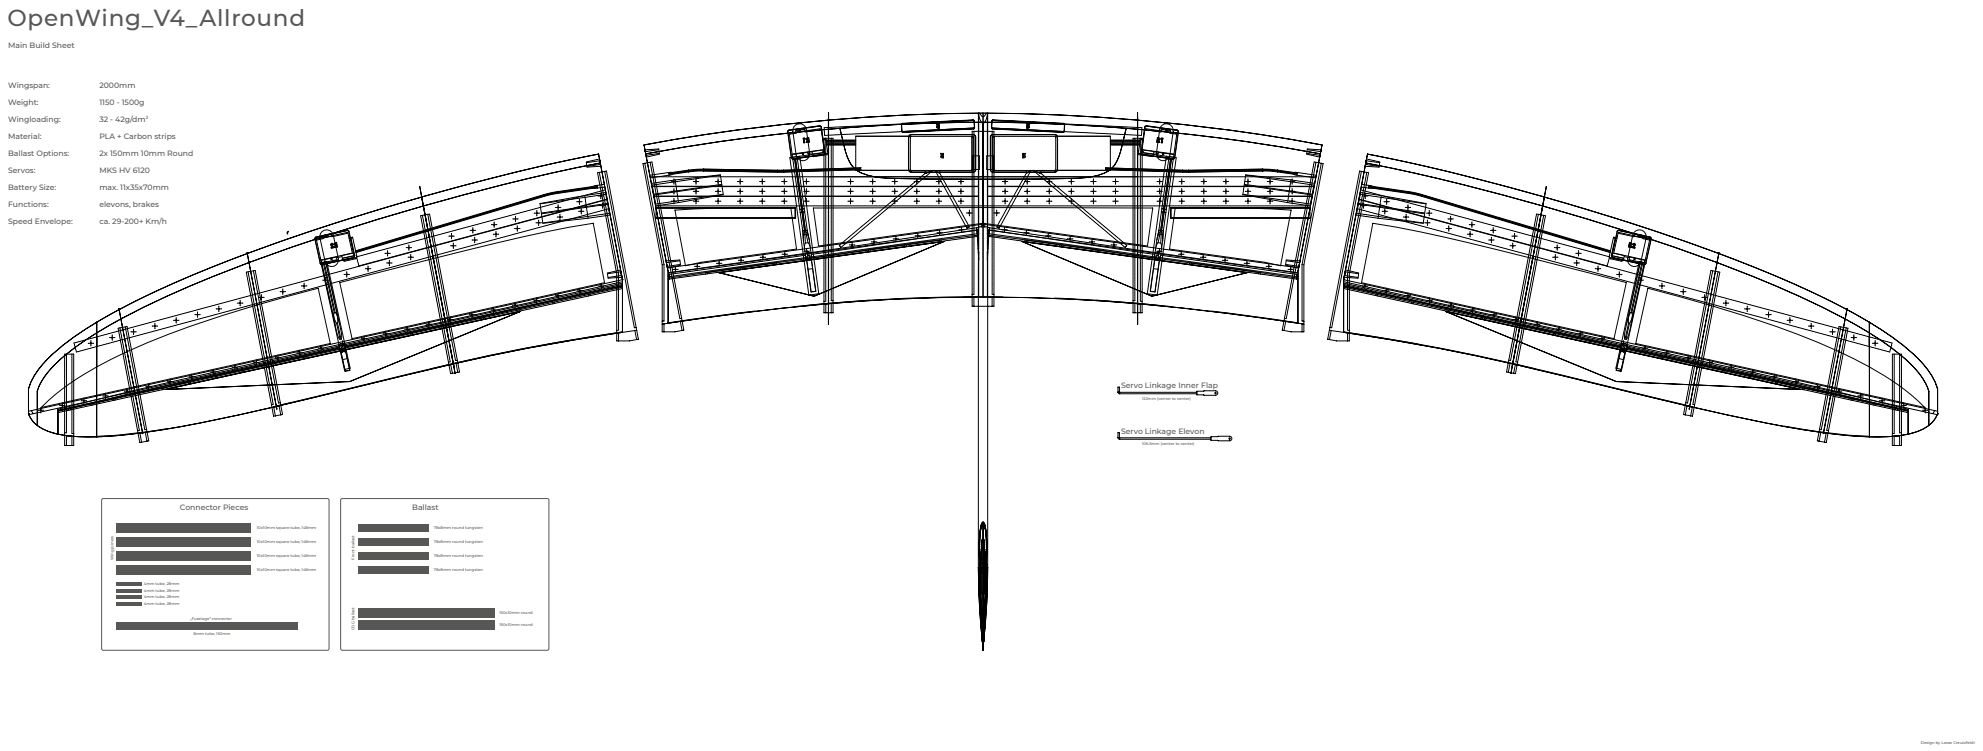
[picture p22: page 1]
Weight:; Wingloading:; Material:; Ballast Options:; Servos:; Battery Size:; Functions:; Speed Envelope:; 32 - 42g/dm²; PLA + Carbon strips; 2x 150mm 10mm Round; MKS HV 6120; max. 11x35x70mm; elevons, brakes; Ballast; 78x8mm round tungsten; 150x10mm round; Connector Pieces; 10x10mm square tube, 148mm; Wing joiners; 4mm tube, 28mm 4mm tube, 28mm 4mm tube, 28mm 4mm tube, 28mm; 8mm tube, 150mm; „Fuselage“ connector

Main Build Sheet

Servo Linkage Inner Flap

122mm (center to center)

Servo Linkage Elevon

106.5mm (center to center)

Front ballast COG ballast

Design by Lasse Creutzfeldt

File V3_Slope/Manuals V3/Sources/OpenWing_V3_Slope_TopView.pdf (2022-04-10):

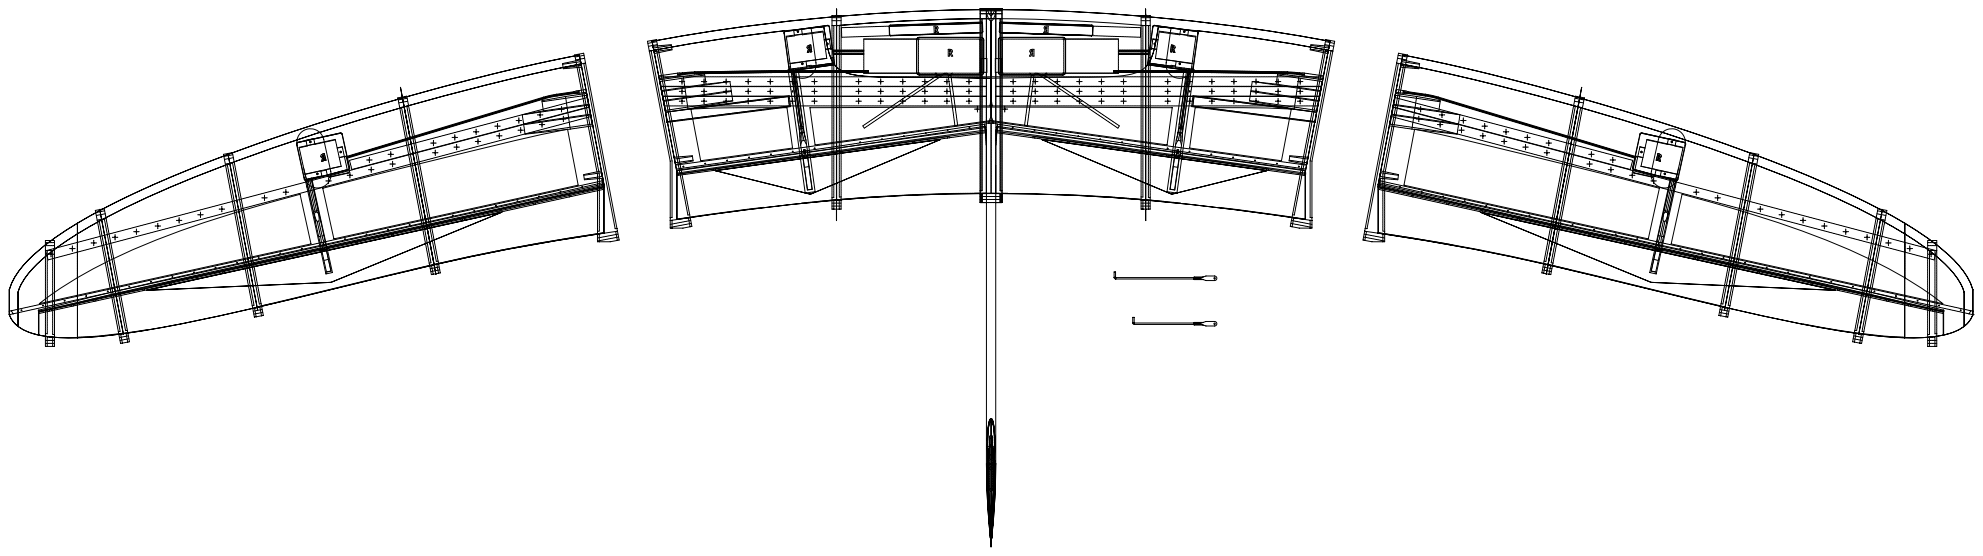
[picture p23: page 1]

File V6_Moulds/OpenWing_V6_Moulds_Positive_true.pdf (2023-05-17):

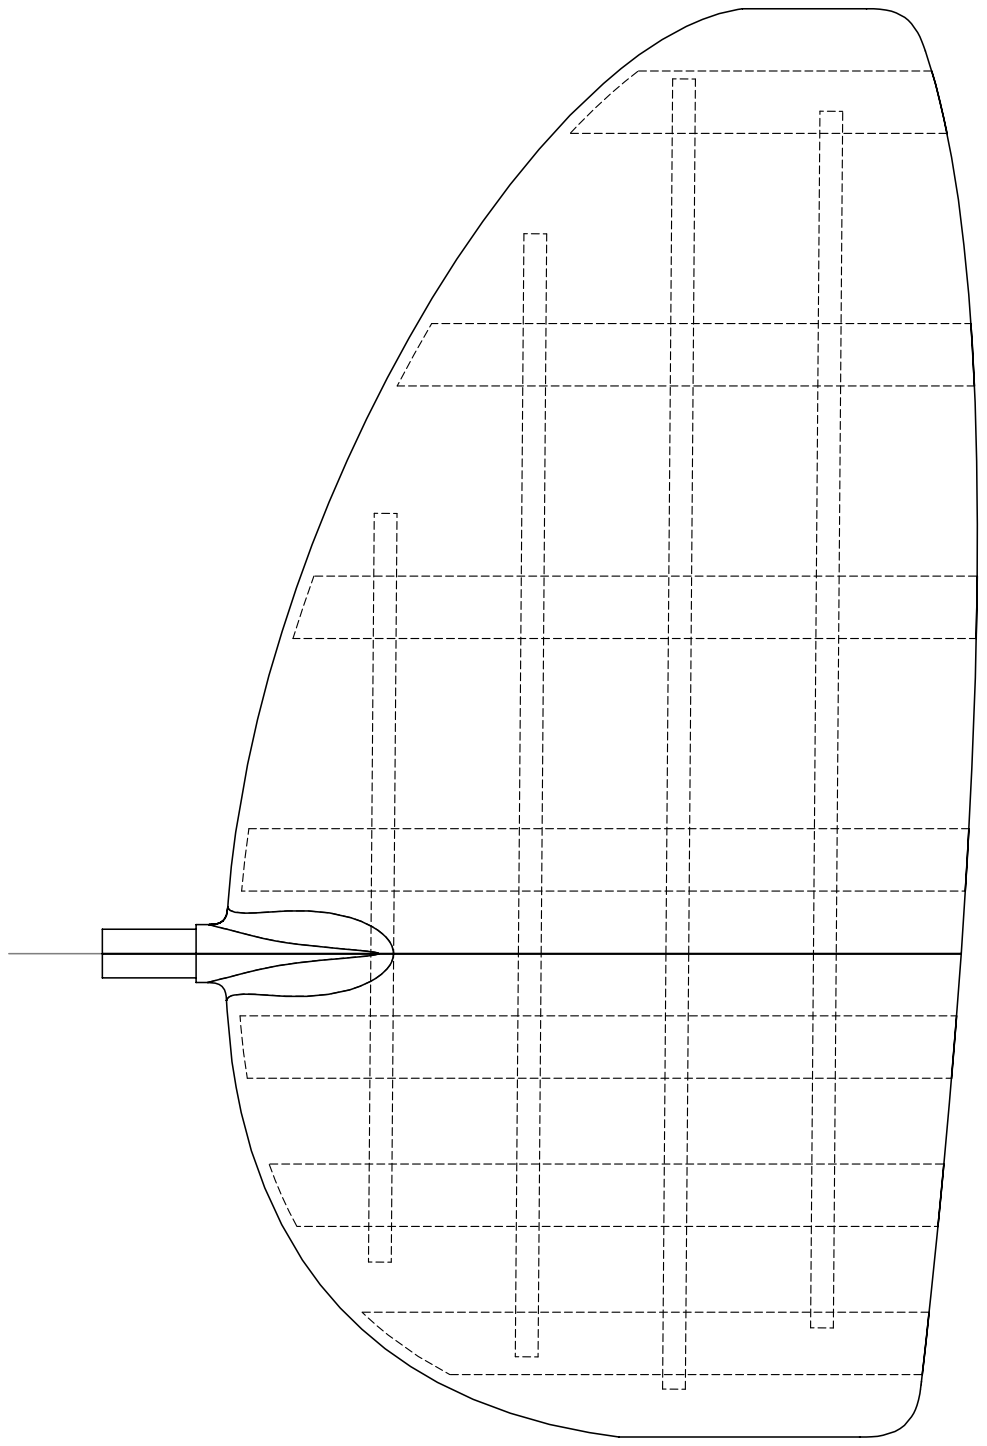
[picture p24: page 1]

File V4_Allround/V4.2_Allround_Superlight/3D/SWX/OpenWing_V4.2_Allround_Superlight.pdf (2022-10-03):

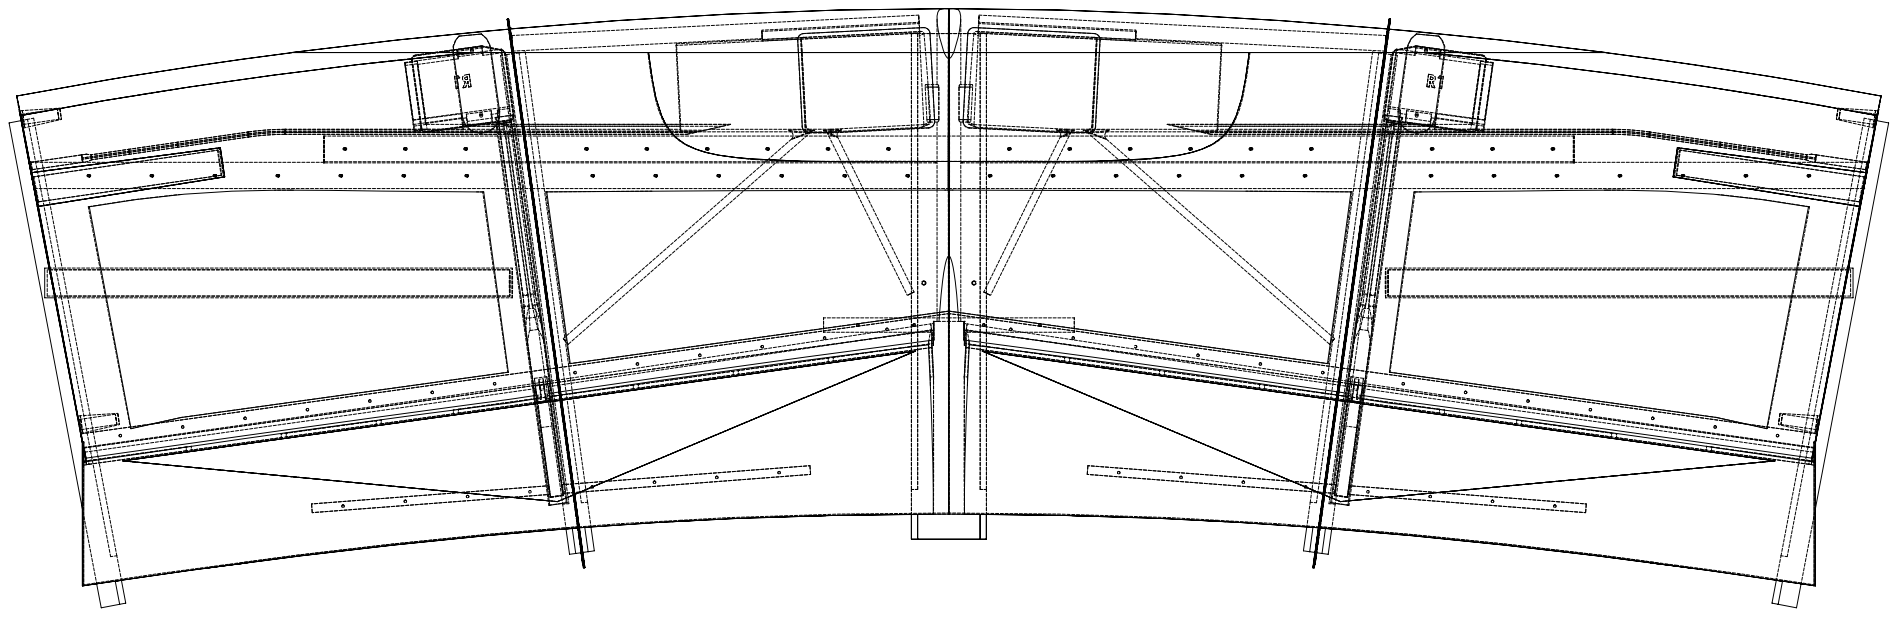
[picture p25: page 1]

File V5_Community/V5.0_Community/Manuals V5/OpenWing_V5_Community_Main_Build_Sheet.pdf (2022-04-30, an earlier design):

# OpenWing_V5_Community

# Wingspan:

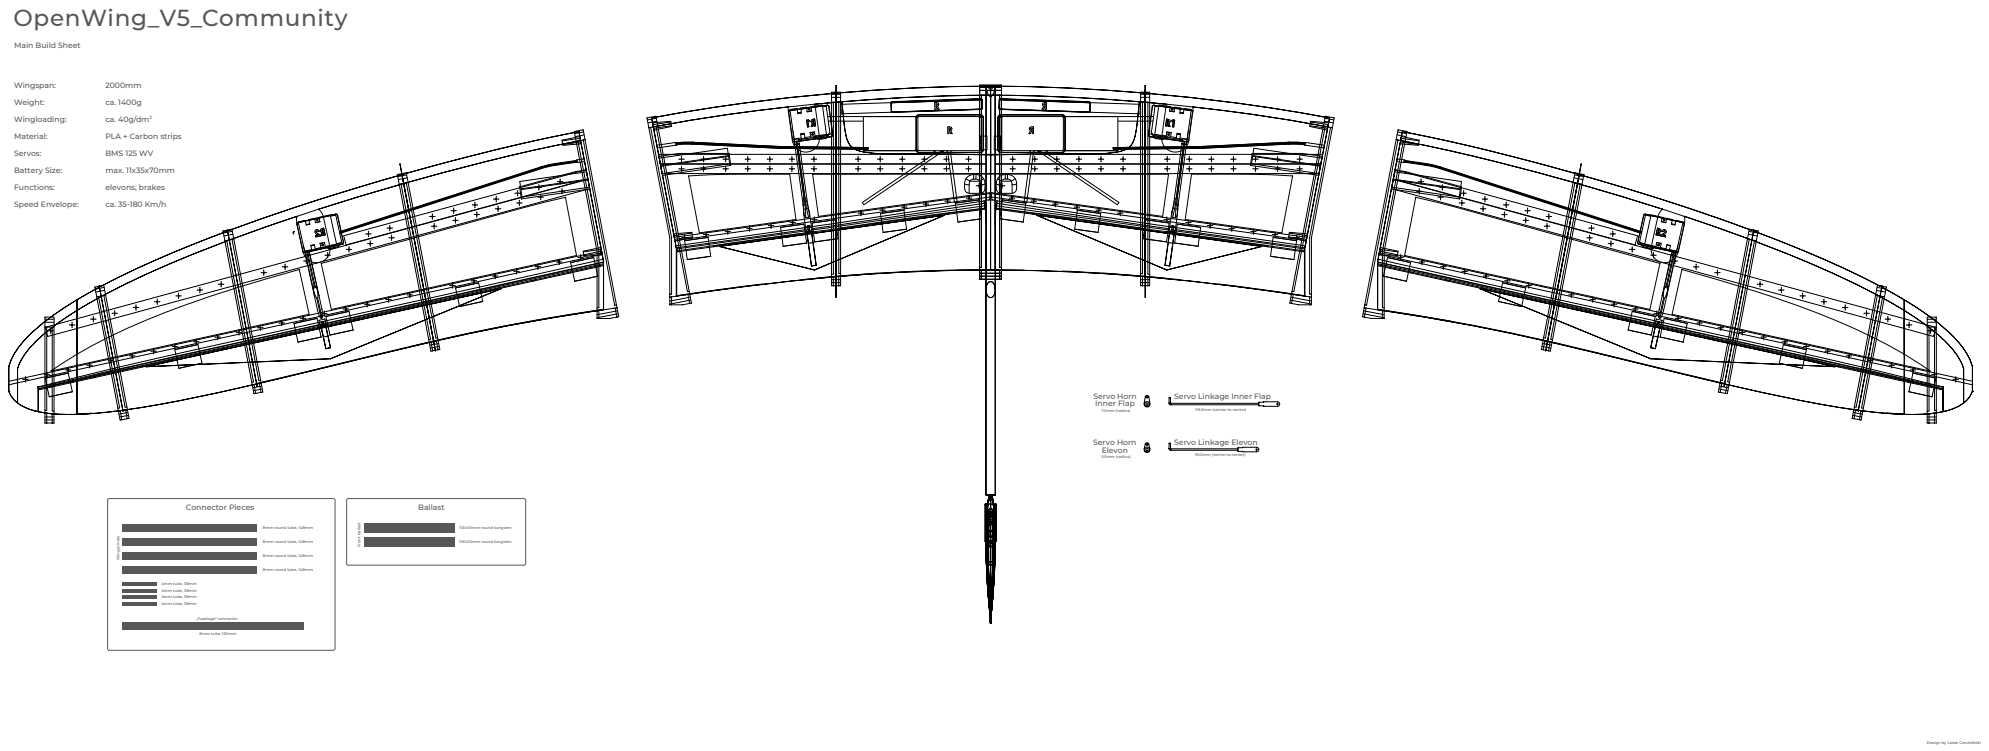
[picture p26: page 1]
Weight:; Wingloading:; Material:; Servos:; Battery Size:; Functions:; Speed Envelope:; Ballast; Servo Horn; Servo Linkage Inner Flap; Inner Flap; 7.5mm (radius); 100x10mm round tungsten; Front ballast; Connector Pieces; 8mm round tube, 148mm; Wing joiners; 4mm tube, 38mm 4mm tube, 38mm 4mm tube, 38mm 4mm tube, 38mm; 8mm tube, 150mm; „Fuselage“ connector

Main Build Sheet

ca. 40g/dm²
PLA + Carbon strips
BMS 125 WV
max. 11x35x70mm
elevons, brakes

118.5mm (center to center)

Servo Horn
Elevon
95.5mm (center to center) 5.5mm (radius)

Servo Linkage Elevon

Design by Lasse Creutzfeldt

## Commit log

2022-04-03 Initial Data Push
    [00.STL, 01.STL, 02.STL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]
2022-04-04 Added .Step Files
    [Open Wing Clean Volume.STEP]
2022-04-05 Changed Project Structure
    [00.STL, 01.STL, 02.STL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]
2022-04-09 Added V3.1
    [Print Settings.xlsx]
2022-04-09 Changed data structure in V3
    [00.STL, 01.STL, 02.STL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]
2022-04-09 Improved V3.1
    [Oso_211231_LC_Mit SLW_V3.1_VS.SLDDRW]
2022-04-10 Updated V3_SLope and added documentation
    [00.STL, 01.STL, 02.STL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]
2022-04-11 Renamed V3 to V3_Slope
    [CCR10_Oso_RrightRibs.3mf, CCR10_Oso_V3_Rudercover aussen.3mf, CCR10_Oso_V3_Ruderhorn aussen.3mf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]
2022-04-12 Renamed to fix links
    [CCR10_Oso_RrightRibs.3mf, CCR10_Oso_V3_Rudercover aussen.3mf, CCR10_Oso_V3_Ruderhorn aussen.3mf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]
2022-04-13 V3_Slope Completely sliced with GCodes
    [CCR10_OpenWing_V3_Slope_ControlHorns.3mf, CCR10_OpenWing_V3_Slope_Covers.3mf, CCR10_Oso_RrightRibs.3mf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]
2022-04-15 Updates on Printsettings and G-Codes
    [Print Settings.xlsx]
2022-04-16 Started on V5_Convenience
    [Bluebird_Servotest.STL, OpenWing_V5_Convenience_220415.STL, Print Settings.xlsx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]
2022-04-24 V5 Almost Ready
    [Bluebird_Servotest.STL, OpenWing_V5_Convenience_220415.SLDDRW, OpenWing_V5_Convenience_220415.STL]
2022-04-27 Subfolders do make PDFs more accessible
    [Print Settings.xlsx]
2022-04-27 Create Currently working on...
2022-04-27 Rename Currently working on... to Currently working on...md
2022-04-27 Update Currently working on...md
2022-04-27 Rename Currently working on...md to Working on | Known Issues.md
2022-04-29 Updated V4_Allround
    [CCR10_OpenWing_V3_Slope_ControlHorns.3mf, CCR10_OpenWing_V3_Slope_Covers.3mf, CCR10_Oso_V4_SLW.3mf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]
2022-04-30 Renaming of V5, slicing errors on V3 inner wing fixed,
    [Ballastdeckel_R.STL, Komponentendeckel_R.STL, OpenWing_V3_Slope.SLDDRW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]
2022-04-30 Exported STLs of V5_Community Main Wing
    [OpenWing_V5_Community_R00.1.STL, OpenWing_V5_Community_R00.2.STL, OpenWing_V5_Community_R00.3.STL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]
2022-04-30 CuraFiles and GCodes for V5
    [OpenWing_V5_Community_Ballastcover.STL, OpenWing_V5_Community_Componentcover.STL, OpenWing_V5_Community_SmallParts.3mf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]
2022-04-30 Added Testpiece in STLs
    [OpenWing_V5_Community_Testpiece.STL, Print Settings.xlsx]
2022-04-30 Added the Helling for V5
    [OpenWing_V3_Slope_HR00.STL, OpenWing_V3_Slope_HR01.STL, OpenWing_V3_Slope_HR02.STL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]
2022-05-31 Klappenschablonen hinzugefügt
    [Invisible2m_AR11-03_V2_STM3fl0cl0134_cl0777max3_33_BW.CSV, Invisible2m_AR11-03_V2_STM3fl0cl0134_cl0777max3_33_BW.xlsx]
2022-06-03 Added Servo Holders
    [Servo_Holder.stl]
2022-07-03 Added V4.1 and V4.2
    [Ballastdeckel_R.STL, Komponentendeckel_R.STL, OpenWing_V4.1_R00.1.STL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]
2022-07-04 Finished V5.1
    [OpenWing_V3_Slope_HR00.STL, OpenWing_V3_Slope_HR01.STL, OpenWing_V3_Slope_HR02.STL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]
2022-10-03 Corrected slicing errors on V5_R01 and V5_R03
    [CCR10_OpenWing_V4.3_Allround_Superlight_Cover.3mf, OpenWing_V4.2_Allround_Helling3°_R00.STL, OpenWing_V4.2_Allround_Helling3°_R01.STL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]
2022-11-20 Sorted V4.3
    [CCR10_OpenWing_V4.3_Allround_Superlight_Cover.3mf, OpenWing_V4.2_Allround_Helling3°_R00.STL, OpenWing_V4.2_Allround_Helling3°_R01.STL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]
2022-11-20 Reorganized Files
    [Ballastdeckel_R.STL, CCR10_OpenWing_V4.3_Allround_Superlight_Cover.3mf, Invisible2m_AR11-03_V2_STM3fl0cl0134_cl0777max3_33_BW.CSV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]
2023-05-17 Changed the moulds
    [CCR10_OpenWing_V6_Moulds.3mf, OpenWing_V4.3_Allround_Superlight_Servohorn R1.STL, OpenWing_V4.3_Allround_Superlight_Servohorn R2.STL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]
2023-05-17 Added Step for Moulds
2023-05-19 Added .STEP for moulds
2023-06-12 Added Clean Volume with 0.3mm TE
    [00.STL, 01.STL, 02.STL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]
